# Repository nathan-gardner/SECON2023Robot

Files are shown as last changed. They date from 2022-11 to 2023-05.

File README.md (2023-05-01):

# **SECON2023Robot - IEEE SoutheastCon Robotics Competition**

## **Final CAD Model for Competition Robot**

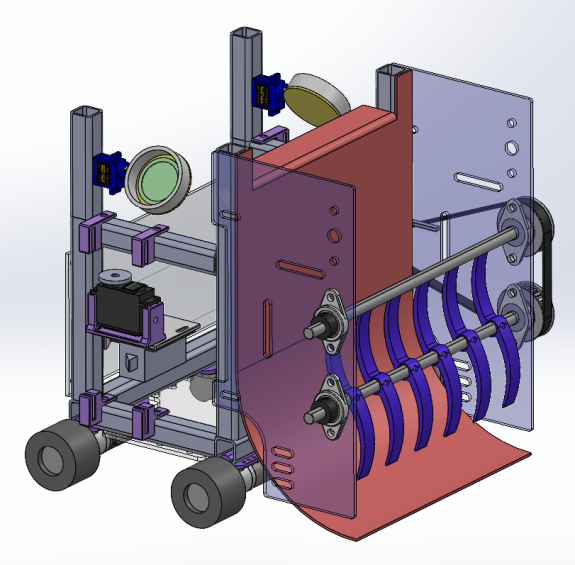
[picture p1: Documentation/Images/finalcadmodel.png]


## **Executive Summary**

The purpose of this project is to build a robot that will be sent to the SoutheastCon student competition in Orlando, Florida. This robot will represent Tennessee Technological University to schools around the Southeastern United States. This document will include further details on the team’s design for the project.

The autonomous tasks the robot may attempt include the following: Feed manatees and alligators the correct food chips, relocate ducks to the duck pond, rebuild pedestals into statues, deposit any unused objects into the recycle bin, and play an animated fireworks video at the end of the round.

The robot was rescoped throughout the year and just before the competition to be able to meet objective and once we know opponents capabilities at the competition. The final robot implemented was able to feed manatees and alligators the correct food chips, relocate ducks to the duck pond, and to push remaining items to the recycling areas. 

The team placed fourth out of thirty six schools in the competition, which is the second best performance in Tennessee Tech history. The team sees this as a success considering the ordering setbacks experienced by all the Capstone teams during the Spring 2023 semester, and the scope changes that were necessary to meet deadlines for the competition. 

Full rules document available [here](/Documentation/IEEE-SoutheastCon-2023-Hardware-Competition-Rules-v3.0.pdf).

## **Capabilities**

The [signoffs](/Documentation/Signoffs/) include function of the subsystem, constraints, buildable schematics, analysis, and bill of materials.

Capabilities of this project are described in signoffs with clear indication of what subsystem progressed through the research phase, which made it into development, and which subsystem were implemented into the robot which went to competition.

The path that this robot follows is defined in [top_level.py](/Software/top-level/top_level_package/scripts/top_level.py) and is all relative to the starting area. The distance is measured using encoder clicks and directions are published within the ROS computation graph. This means the robot cannot observe its surroundings and react to its surroundings, but can only go point to point based on the code within that top_level.py file. This was fine for our street sweeper implementation, and was a necessity in design because none of our vision sensors that we ordered came in the mail. This path implementation was reliable across runs. The direction publications were formatted as ROS Twist messages which gave direction and velocity in rotations per minute. The RPM was maintained on the Arduino using a custom PID controller written in C++. 

## **Salient Outcomes**

The team believes that one salient outcome of this project is a platform for understanding robot operating system for future SECON competitions at Tennessee Tech, and other robotics projects undertaken by capstone groups at the University. This is specifically referring to the TCP/IP network communication established in this project between the Jetson Nano and Arduino Mega2560. 

This project was the closest ever integration of the Mechanical Engineering Department's Senior Design course and the Electrical and Computer Engineering Department's Capstone course. These courses are based around an all-encompassing project from what students have learned in University. The team and its advisors has learned a lot about what has worked and what can be improved with this format of project, and this lessons learned will be taken into the future with the students graduating and for those advisors with future groups.  

## **Project Demonstration & Images**

### **Video of Robot at Competition**

Video of robot at competition during the first round of semi-finals available [here](https://www.youtube.com/watch?v=IqyCZeEZ9IM).

### **Robot image**

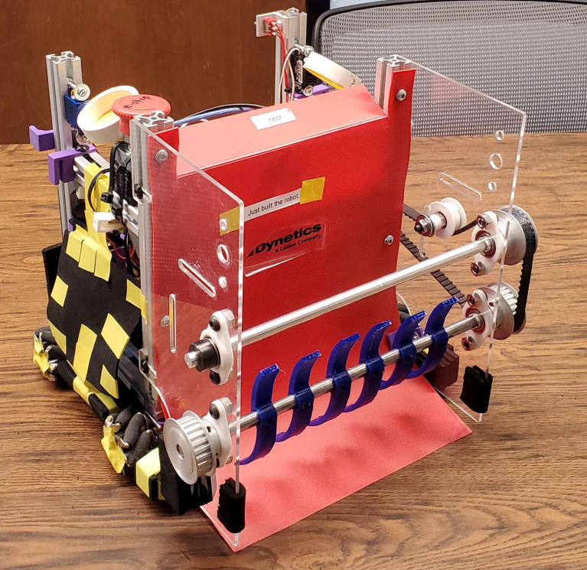
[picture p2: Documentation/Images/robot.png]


More images of the robot available [here](/Documentation/Images/robot/).

#### **Description of Arena:**

- Feeding areas - green and red rectangles in the left corners of the arena
- Starting area - White square in the bottom center of the arena
- Duck Pond - Blue circle in the middle of the top section of the arena
- Recycling areas - Striped white rectangles in the right corners of the arena
- Fireworks switch - Silver rectangle on the right side of the arena
- Inner circles - Three located to the left and right of the starting area, as well as in the middle of the duck pond

#### **Areas utilized for points during competition**

- Feeding areas - Most of our teams points came from correctly delivering the food chips to the feeding areas consistently.  
- Recycling areas - Where the robot pushed loose and randomly placed items to gain points. 
- Duck pond - Ducks ended up in the duck pond during competition. This counted for points on the scoreboard. 

## **Subsystems**
- [Feeding](/Documentation/Signoffs/LukeMcGill-signoff-Feeding.md) - Delivered chips to correct area using servos.
- [Locomotion](/Documentation/Signoffs/LukeMcGill-signoff-Locomotion.md) - Transported robot using mecanum wheels.
- [Power](/Documentation/Signoffs/MarkBeech-MadisonKelly-signoff-Power.md) - Powered every system with two 6V batteries and a 12 V battery.
- [Low-level Controller](/Documentation/Signoffs/NathanGardner-signoff-LowlevelController.md) - Arduino Mega2560 was selected as the main motor controller. 
- [Top-level Controller](/Documentation/Signoffs/NathanGardner-signoff-ToplevelController.md) - Nvidia Jetson selected for computation power as compared to Raspberry Pi.
- [Delivery System](/Documentation/Signoffs/Team2-signoff-ConsumptionSubsystem.md) - pushed objects outward when near a recycling area.

## **Cut Subsystems with explanation**
- [Vision](/Documentation/Signoffs/Fatima-signoff-vision.md) - Sensors were not received in time for building. The team ordered LIDAR sensor and color sensors and they never arrived.
- [Duck Storage](/Documentation/Signoffs/MadisonKelly-signoff-DuckStorage.md) - Subsystem cut as part of the rollback a few days before the competition. We did not have consistency in delivering the ducks stored to the duck pond reliably. A risk reward analysis was done and it was voted on by the team to remove the subsystem entirely. 
- [Pedestal Storage and Delivery](/Documentation/Signoffs/MadisonKelly-signoff-PedestalStorageAndDelivery.md) - Parts were not received in time for building. 
- [Sorting](/Documentation/Signoffs/MarkBeech-signoff-Sorting.md) - Parts were not received in time for building. Sorting was cut when rescoping once we realized we were not receiving parts for many of the subsystems we ordered. 
- [Consumption -> Delivery Subsystem](/Documentation/Signoffs/Team2-signoff-ConsumptionSubsystem.md) - Rescoped 24 hours before the competition. The function was transitioned from consumption into the robot to ejection into the recycling area.  

## **Experimentation**

For each run, there were ten ducks and seven pedestals randomly distributed on the arena as well as six food chips (3 red and 3 green) that the team could pre-load before the run started. The team had three minutes after the start switch was flipped to get as many points as possible. The results from these runs are shown below.



| Round | Green chip | Red chip | Cylinder Recycle | Duck Recycle | Duck Pond | Grand Total Points |
| ----- | --- | --- | --- | --- | --- | --- |
| 1 | 3 | 3 | 1 | 4 | 0 | 52 |
| 2 | 3 | 3 | 0 | 0 | 0 | 42 |
| 3 | 2 | 3 | 0 | 0 | 0 | 35 |
| 4 | 2 | 2 | 4 | 6 | 0 | 48 |
| 5 | 3 | 3 | 4 | 1 | 0 | 52 |
| 6 | 2 | 2 | 1 | 2 | 1 | 39 |

Below is the number of points scored in each round of the competition. If we had integrated the all functionality targeted after the rescope, we would have scored 86 points each round. 

Recycling: $2\ points * 17\ objects = 34\ points$

Feeding: $6\ correct chips * 7\ points = 42 \ points$

Fireworks: $1\ fireworks\ switch\ flip * 10\ points = 10\ points$

Total: $86\ points$



**Full experimentation document available [here](https://github.com/nathan-gardner/SECON2023Robot/blob/main/Reports/Experimentation.md).**

## **About Us**

### **Team Image**



**Names from left to right:** Grayson Vermillion, Carlos Salvatierra, Ethan Lewis, Mark Beech, Luke McGill, Nathan Gardner, and Madison Kelly.

### **IEEE Hardware Team**

**ECE team**

Nathan Gardner is an undergraduate Computer Engineering student and is currently a Senior at Tennessee Technological University. Nathan is Team Lead/ Captain for the Southeastcon Robotics Competition Hardware Team. Nathan was responsible for the low-level and top-level controller subsystems and worked on most of the  software implementation for the robot. 

Madison Kelly is an undergraduate Electrical Engineering students and is currently a senior at Tennessee Technological University. Madison is the Project Manager for the Southeastcon Robotics Competition Hardware Team. Madison was responsible for the storage subsystems and was partially responsible for the power subsystem along with Mark Beech.

Fatima Al-Heji is an undergraduate Computer Engineering student and is currently a senior at Tennessee Technological University.

Luke McGill is an undergraduate Electrical Engineering student and is currently a Senior at Tennessee Technological University. Luke was responsible for the locomotion and feeding subsystems. Luke also worked on the software implementation for the robot.

Mark Beech is an undergraduate Electrical Engineering student and is currently a senior at Tennessee Technological University. Mark was responsible for the sorting subsystem and was partially responsible for the power subsystem along with Madison Kelly.

**ME team**

Grayson Vermillion

Carlos Salvatierra is an undergraduate Mechanical Engineering student at Tennessee Technological University. Carlos is a member of the Southeastcon Robotics Competition Hardware Team. Carlos is responsible for creating the robot chassis and drivetrain. Carlos has years of experience working with and leading various high level robotics teams in the past.

Ethan Lewis

### **Faculty Supervisor**

Mr. Jesse Roberts

### **Stakeholders**

The Institute of Electrical and Electronics Engineers (IEEE) is the organization that is hosting the competition in Orlando, Florida on April 13-16th, 2023. Stephen Hopkins is the chair of the hardware competition. Tommy Dillen from Valencia College is the leader of Valencia IEEE Student Chapter design team and designed the arena for the competition.

At the competition, the team will represent the Tennessee Tech ECE Department by showing the skills acquired over most of the ECE curriculum.

Tennessee Technological University's College of Engineering's reputation will be affected by our presence and performance at the competition.

## **Repo Organization**

Below is the layout of the repo.

### **Reports**

Reports are attached in the Reports folder, linked below, and are named "Team2_(NameOfDocument)".

[Reports](/Reports/)

### **Documentation**

The [3D Models](/Documentation/3D%20Models) folder contains any CAD models there might be.

The [Electrical](/Documentation/Electrical) folder contains all electrical schematics.

The [Images](/Documentation/Images) folder contains images of the subsystems.

[Signoffs](/Documentation/Signoffs) folder contains the completed signoffs for each subsystem.

##### **Main Documentation Folder**

[Documentation](/Documentation/)

### **Software**

We will use language and Google (.clang-format) standard programming practices when writing software. We will document our code using Doxygen markdown and commenting style for readability. 

[Software](/Software/)

_Note: This repository was publicly archived on April 30th, 2023_

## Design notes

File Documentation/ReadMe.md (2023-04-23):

# Documentation

## Signoffs

Signoffs are the detailed design documents for the project. They include detailed specification, buildable pdf schematic, analysis, and the bill of materials. Analysis is performed on components to prove that they are sufficient and will likely work. The signoffs that are in main have been approved by the supervisor, Mr. Jesse Roberts. Signoffs are included in a marddown file [here](/Documentation/Signoffs/). 

## Final set of prints (final design artifacts)



### 3D Models

3D models are included [here](/Documentation/3D%20Models/).

The 3D models section will be updated throughout the project to reflect what has been signed off and designed. 

### Wiring Schematics

Electrical wiring schematics available [here](/Documentation/Electrical/Schematics/).

The wiring schematics section will be updated throughout the project to reflect what has been signed off and designed. 

#### PCB files

Electrical wiring PCBs available [here](/Documentation/Electrical/PCB/).

The PCB files section will be updated throughout the project to reflect what has been signed off and designed. 

## Final BOM

Final BOM available [here](/Documentation/BOM/TotalBOM_Final.pdf).

## Datasheet 

Each subsystems datasheet is essentially the signoff for that subsystem. The final datasheet will be created near the end of the project when the design is complete.

Final Datasheets for each subsystem available [here](/Documentation/Signoffs/).

## The project poster

Final poster available [here](/Documentation/Poster/IEEE%20SECON%20Hardware%20Competition%20Team%20Final%20Poster.pdf).

## Detailed photos of the project

Detailed photos for the project are available [here](/Documentation/Images/).

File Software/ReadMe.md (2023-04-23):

# Software

Project source code is stored here. Below is an explanation of each file and how it functioned in the project.

Further documentation on each project can be found in comments/doxygen in the source code. 

## **Files**
- [demo](/Software/demo/) - Initial PlatformIO project created in testing. This was used to setup ROSSerial and to confirm that we would be able to use ROSSerial to pass messages between the Nvidia Jetson and the Arduino Mega as we had planned in design.
- [matlab-sim](/Software/matlab-sim/) - File for MATLAB simulations used during signoffs
- [mega2560](/Software/mega2560/) - PlatformIO Project that ran on the Arduino Mega during the competition. Mega functioned as the main motor controller and hardware interface device for this project.
- [top-level](/Software/top-level/) - ROS package with holds the script that ran on the Nvidia Jetson to command the robot to follow its path in the arena and actuate motors.
- [ultrasonic](/Software/ultrasonic/) - Ultrasonic demo that was created while the team was considering implementing ultrasonic in the project.

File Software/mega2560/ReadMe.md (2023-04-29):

# mega2560/mega1

## Software Function

PlatformIO Project that ran on the Arduino Mega during the competition. Mega functioned as the main motor controller and hardware interface device for this project.

## Dependencies

Operating system: 22.04.1-Ubuntu
IDE: VSCode
Extensions: PlatformIO
Required installations: ROS Melodic, rosserial

## How to Install

Step by step instructions for installation can be found below:

[VSCode](https://code.visualstudio.com/Download)

[ROS Melodic Installation](http://wiki.ros.org/melodic/Installation/Ubuntu)

[ROSSerial Installation](https://sites.duke.edu/memscapstone/using-rosserial-to-setup-a-ros-node-on-a-teensy/)

## Program Execution

This is a PlatformIO project and code can be uploaded to the Arduino using the upload button (->) on the command bar of at the bottom of the VSCode window. 



The following code is executed on the Nvidia Jetson (or comparable computer) to execute this program

```
# start ros master
roscore

# start rosserial
rosrun rosserial_python serial_node.py _port=[PATH_TO_ARDUINO_PORT] _baud=115200

# to start main top_level.py execution, navigate to top_level.py and run with python command
cd [PATH_TO_REPO]/Software/top-level/top-level-package/scripts
python top_level.py
```

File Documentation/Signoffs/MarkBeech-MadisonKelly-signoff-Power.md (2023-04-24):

# **Power Subsystem**
## **Function of The Subsystem** 
- Provides power to all other subsystems that require voltages and currents not supplied indirectly through the low-level controllers or the top level controller pins.
- Allows the robot to be turned off and on.
- Addition of an emergency stop button in order to meet safety standard and competition requirement.
## **Constraints** 
- The power supply must supply 12 V and a current of more than 2 A to accommodate all components that will be running at one time. 
- The output of the battery must be regulated with a DC-DC converter in order to ensure each component is provided with the proper voltage for operation.   
- Fuses will need to be added to the power supply bus for added overcurrent protection.
- Many of the loads will need to be stepped down to 6V and have a regulated output to eliminate ripple voltage. There will be filters to smooth out the ripple
- The ripple voltage from the inductive load of the motors should be eliminated in order to protect other components. To mitigate this, the team will add smoothing capacitors on each motor load.
- Voltage input ranges for all components can be seen in the table below.
- Since there are multiple loads that need 12V and 6V supplied, there will need to be a power bus for each of them. The power bus selected is rated up to 10A.
- The power supply chosen has a 5V USB output. Because of this, the concerns for powering the Nvidia Jetson as well as both arduinos will be separate from the remainder of the components. 
- An emergency stop button must be used for the safety of those involved in the competition. 
  - The emergency button must have a flyback diode attached in reverse bias because of the motor’s inductive load and the chance of a sudden switch in the power being supplied.

### **Constraint from Standard**

- Shall have a self-latching emergency stop push-button that has a positive operation. The button shall not be a graphical representation or a flat switch based on NFPA 79 - 10.7.2.

### **Voltage input ranges for all components**

| Component | Input Range |
| --- | --- |
| DC-DC converter | 9V to 18V |
| Buck Converter board  | 4.0 to 40V  |
| L298N | 5V to 35V |
| TB9051FTG | 4.5V to 28V |
| Micro Maestro | 5V  to 16V  |
| Lock style solenoid | 9V to 12V |
| Nvidia Jetson nano | 4.75 V to 5.25 V |

### **Voltage and current requirements for all components**

| Subsystem | Component | Voltage (V) | Current (A) |
| --- | --- | --- | --- |
| Locomotion | Motor Drivers (2) | 12 | 1.2 |
| Consumption | Motor Driver | 6 | 0.5 |
| Duck Storage and Delivery | Solenoid Actuator | 12 | 0.65 |
| Pedestal Storage, Duck Storage, Sorting, and Feeding | Servo Motor Controller | 6 | 2.17 |
| Sorting | Motor Controller | 6 | 0.25 |

### **Voltage and current requirements for all continuous components**

| Subsystem  | Component | Voltage (V) | Current (A)  |
| --- | --- | -- | ---- |
| Locomotion  | Motor Drivers - Motors (4) | 12 | 1.2  |
| Consumption | Motor Driver - Motor | 6  | 0.5  |
| Sorting | Motor Controller | 6  | 0.25 |

## **Buildable Schematic**

### **CAD Model for the subsystem:**

Shown below is the layout of the robot. The compact size of this power supply (shown in red) should allow for plenty of room for other components as needed.



### **Electrical Schematics:**

All electrical circuits will be implemented via soldered breadboard.

**Initial electrical schematic**



**Final implementation electrical schematic**



## **Analysis**

### **Power Supply - 12V Output** 

The power supply can supply 12 V at 6000 mAH and 5 V at 12000 mAH and the maximum current output is 3A. Since each competition round is only 3 minutes, the following calculations were performed. 

$Time = \frac{6000\ mAh}{3\ A} = 2\ hours = 120\ minutes$

$rounds = \frac{120}{3} = 40 rounds$

The robot should be able to run up to 40 rounds without needing a charge. This will help with testing as well as reducing the risk that the robot's power supply will die during the competition.

### **Current Analysis**

#### **Block Diagram for all components**



Currents have been labelled for use in a matlab script detailed below. Each current value listed by each component was found from the components datasheet.

#### **Block diagram for all constant loads**



#### **Matlab Simulation**



This simulation was done using the block diagram for all constant loads shown above.

This calculates the currents going into each branch and adds them together to find the total current needed to be supplied by the power supply. This was done while taking into account the efficiencies of the buck converter and the DC-DC converter.

According to the MatLab simulation above the total current needed to be supplied by the power supply is 1.767 A. The power supply chosen has a max output current of 3 A, which is almost double the constant current constraint.

### **DC-DC Converter**
This power supply has an output range from 9 - 12.6 V with a typical value of 11.1 V. This is why a DC-DC converter is needed to regulate the input to 12 V. The concern for noise produced by the buck converter is adressed in an LTSpice simulation shown below.

The power supply itself has a ripple of 100 mV, which is not a problem for this DC-DC converter as it can accept anywhere between 9 - 18 V.



According to the datasheet for the DC-DC converter chosen, the ripple noise has a peak to peak ampliture of 150 mV and a switching frequency of 270 kHz. The noise has been modelled as such and can be seen in the LTSpice model above (This noise was measured by the manufacturer with a $1 \ \mu F$ ceramic capacitor in parallel with a $10 \ \mu F$ electrolytic capacitor, which can be added to the circuit if necessary)



Above is the unregulated noise before passing through the filter. The filter will be implemented via a solderless breadboard.



Above is the output voltage after the filter. The voltage appears to be much claner and varries very close to exactly 12 V.

### **Buck Converters**
The buck converter boards were found on Digi-key. The board uses the LM2596 voltage regulator IC and, according to the datasheet provided by Digi-key for the board, it is suitable for our application.

Noteable specs include:
- Input voltage: 4 - 40 V
- Output voltage: 1.5 - 37 V
- Max output current: 3 A
- Max output power: 20 W
- Switching frequency: 150 kHz
- Adjustable via screw potentiometer
- built in voltmeter

Buck converter boards will be used to drop the 12 V supply voltage to 6 V for all components needing 6 V to operate. These buck converters are shown on the electrical schematic above. 

According to the datasheet for the LM2596 part, a typical output ripple voltage can range from approximately 0.5% to 3% of the output voltage. This means The output ripple at worst case will be:

 $0.03(6) = 0.18 \ V = 180 \ mV$



Above is an LTSpice simulation of the noise ripple that could result from the buck converter board. The device has a switching frequency of 150 kHz as reflected in the model.



Above is the unregulated noise signal with $V_{p-p} = 180 mV$ and a frequency of 150 kHz. A LC filter with a diode will be implemented on a solderless breadboard to flatten out the voltage.



As shown above the output voltage is regulated to 6 V with a small ripple of less than 1% of the output voltage.

### **Motor Ripple**

All motors chosen in this project have come from Pololu. Pololu recommends connecting up to three $0.1 \mu F$ capacitors to the motors. It was recommended that one cap should be connected from the positive lead to the case, one from the negative lead to the case, and one across the input terminals.

### **Power Bus**

Since there are many components that need 12V and 6V, there will be at least two power buses to better distribute the power to the correct components within the robot. The buses selected are rated up to 24V, and 12V is the maximum voltage within the robot. Also, the number of outputs on the bus itself is much greater than the number of outputs the team will need. Therefore, the buses selected will be sufficient. 

### **USB Output Power**

The Nvidia Jetson Nano Dev kit will be power via the USB-A port on the power supply connected to the Jetson's micro USB port. This supply has a ripple of 100 mV on this output as well, meaning the output can be from 4.9 V to 5.1 V per the image below sent from the manufacturer via email. 



The Jetson requires anywhere from 4.75 V to 5.25 V to operate, meaning it can run even with the ripple of 100 mV. As for current, the power supply is rated for up to 2 A, which is what the Jetson requires.

### **Emergency stop button**

The emergency stop button will need to have a flyback diode connected to the two output lines of the button to prevent sudden voltage spikes when current is interrupted.

The E-stop button was chosen to be a 2 channel normally closed switch. This was chosen so power can be broken from locomotion, consumption and sorting all together with one button as shown in the electrical schematic above. 

## **BOM**
| Name of Item | Description | Used in which subsystem(s) | Part Number | Manufacturer | Quantity | Price | Total  |
|---|---|---|---|---|---|---|---|
| Rechargeable 12 V Battery | 12 V/6000 mAH Lithium Ion Battery Pack | Power | YB1206000-USB  | TalentCell | 1 | 39.99 | 39.99  |
| Buck Converters | DC-DC Adjustable Buck Converters 3-40V to 1.5-35V | Power | LM2596 | ATNSINC | 3 | 15.69 | 47.07  |
| E-Stop Button | Self-Locking Emergency Stop Button 2 NC Red Mushroom 660 V 10 A | Power | HB2-BS544 | MXUTEUK | 1 | 10.99 | 10.99  |
| 3 A Fuses | 3A 250V Fuses (pack of 20) | Power | F3AL250V | BOJACK | 2 | 5.99 | 11.98  |
| 1N5822 Diode | Ximimark 100Pcs 1N5822 Schottky Diode 3A 40V DO-201AD (DO-27) Barrier Rectifier Diode for Household Appliances | Power | 1N5822 | Ximimark | 1 | 7.29 | 7.29 |
| 0.1 uF Capacitors | E-Projects - 0.1uF Ceramic Disc Capacitor - 50 Volts (25 Pieces) | Power | 0.1 uF | E-Projects | 1 | 5.99 | 5.99 |
| 1 uF Capacitor | 1 µF Conformal Coated Tantalum Capacitors 50 V Radial 8Ohm | Power | TAP105K050SCS  | KYOCERA AVX | 1 | 0.82 | 0.82 |
| 330 uF Capacitors | Capacitor 4.7UF 6.8UF 10UF 15UF 22UF 47UF 100UF 220UF 330UF 470UF 680UF 1500UF Electrolytic Capacitors Kit 6.3V 10V 16V 25V 35V 50V 100V 400V,295Pcs | Power | 330 uF | changhe | 1 | 18.98 | 18.98  |
| 33 uH inductors | uxcell 50Pcs 0510 Color Ring Inductor 33uH 1W Axial RF Choke Coil Inductor | Power | 33 uH | uxcell | 1 | 8.49 | 8.49 |
| DC-DC Converter | DC DC Converter 12 V 120 W | Power | 209-JCK4012S12 | XP Power | 1 | 71.5 | 71.5 |
| Power Distribution Bus | Solid Brass | Power | 737 | Adafruit | 5 | 1.95 | 9.75 |
| Total | | | | Total Components | 16 | Total Cost | 232.85 |

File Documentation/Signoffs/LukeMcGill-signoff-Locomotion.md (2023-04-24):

# Locomotion Subsystem
## Function of the Subsystem
- Transport the robot no less than 0.0677 m/s

- Ensure that the predetermined path can be traversed in the allotted time of three minutes

- The top level controller communicates with the low level controller through USB. The low level controller will then send a PWM signal to the motor driver, which will control the motor's speed. The low level controller will also send a digital signal to the motor driver that will control the direction of the motor.

## Constraints
- Weight of the robot ( $\approx$ 10.376 kg)
- Minimum travel speed required (0.0677 m/s)
- Motor torque required (0.0604 Nm per motor)

### Socioeconomic Consideration
- Motor chosen will operate at $\approx$ 70% of it's maximum efficiency. This will help conserve power and reduce battery charging costs.

## Buildable Schematics

### Motor


The two motor encoders will tell the low level microcontroller how fast the motor is driving, as well as the direction. These will be used in the path planning process.

### Electrical Schematic
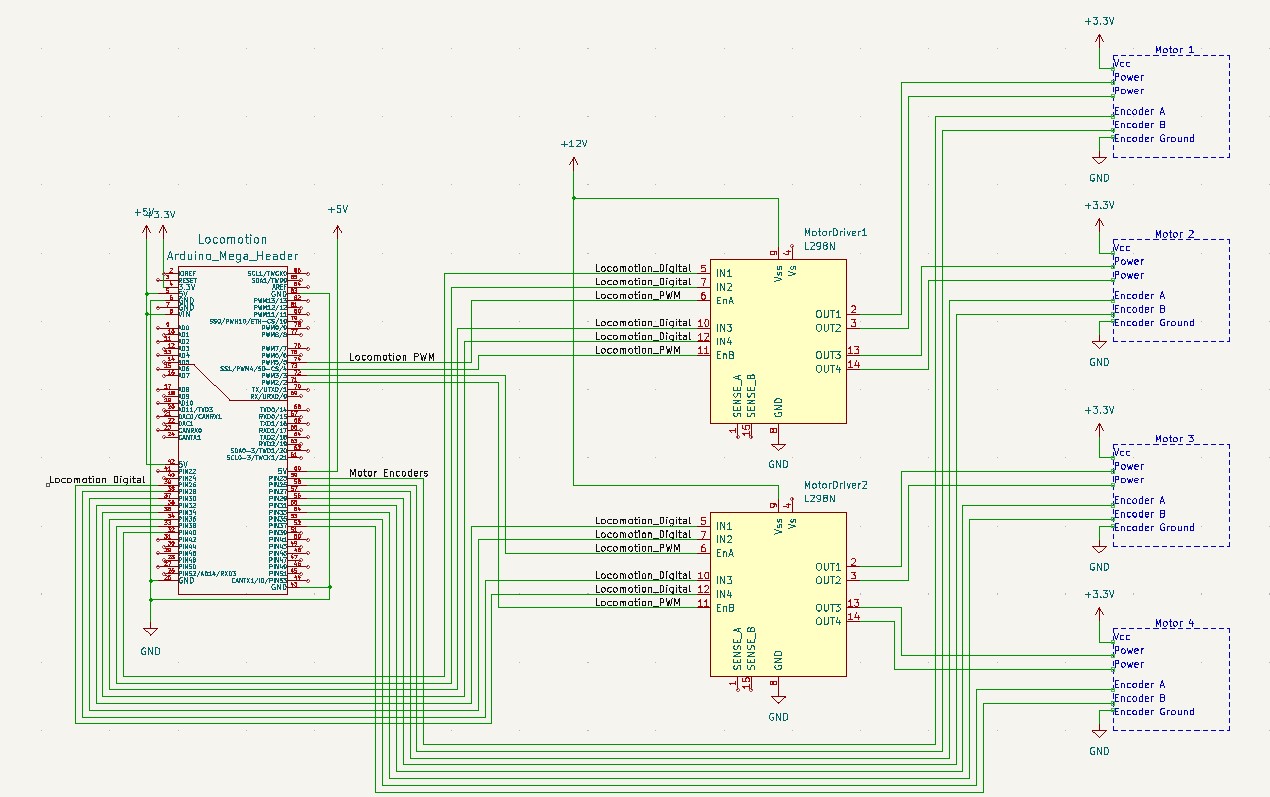
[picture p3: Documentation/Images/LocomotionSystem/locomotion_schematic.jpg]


The electrical schematic can be found [here](https://github.com/nathan-gardner/CapstoneRepo/tree/main/Documentation/Electrical/Schematics/Sources/Locomotion):

### Locomotion Assembly
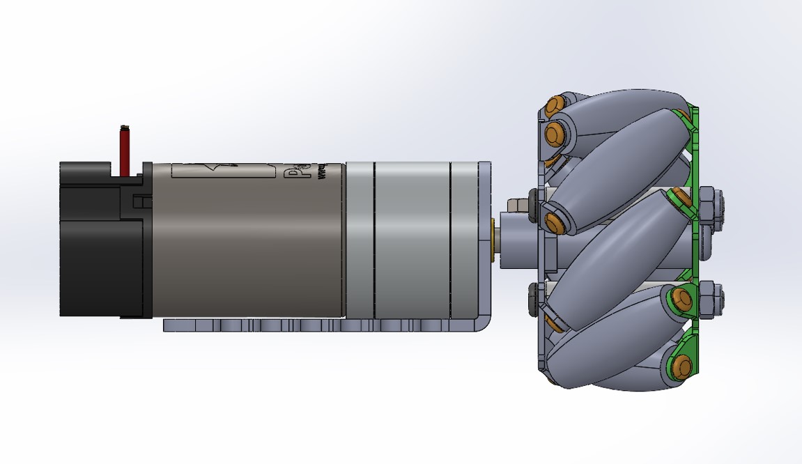
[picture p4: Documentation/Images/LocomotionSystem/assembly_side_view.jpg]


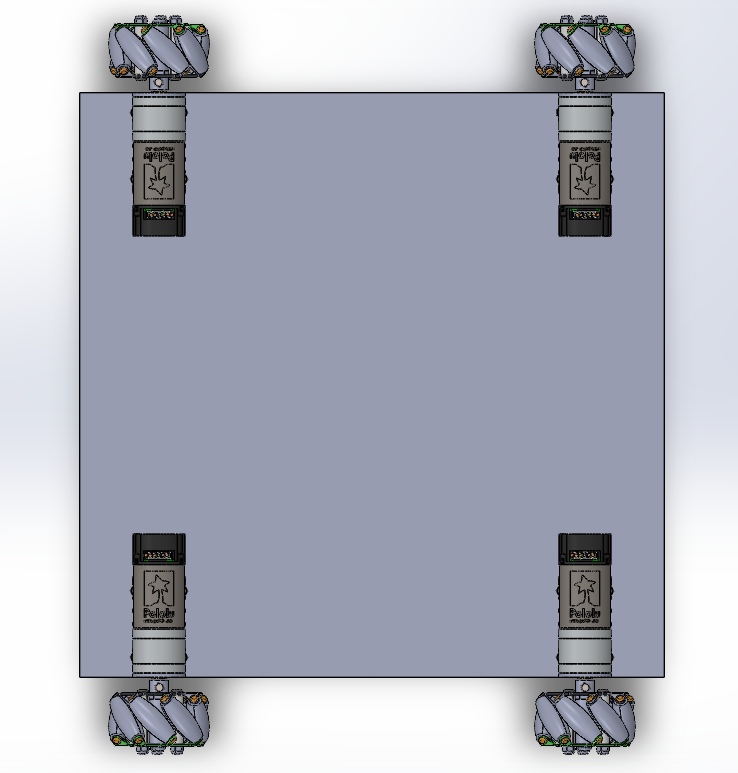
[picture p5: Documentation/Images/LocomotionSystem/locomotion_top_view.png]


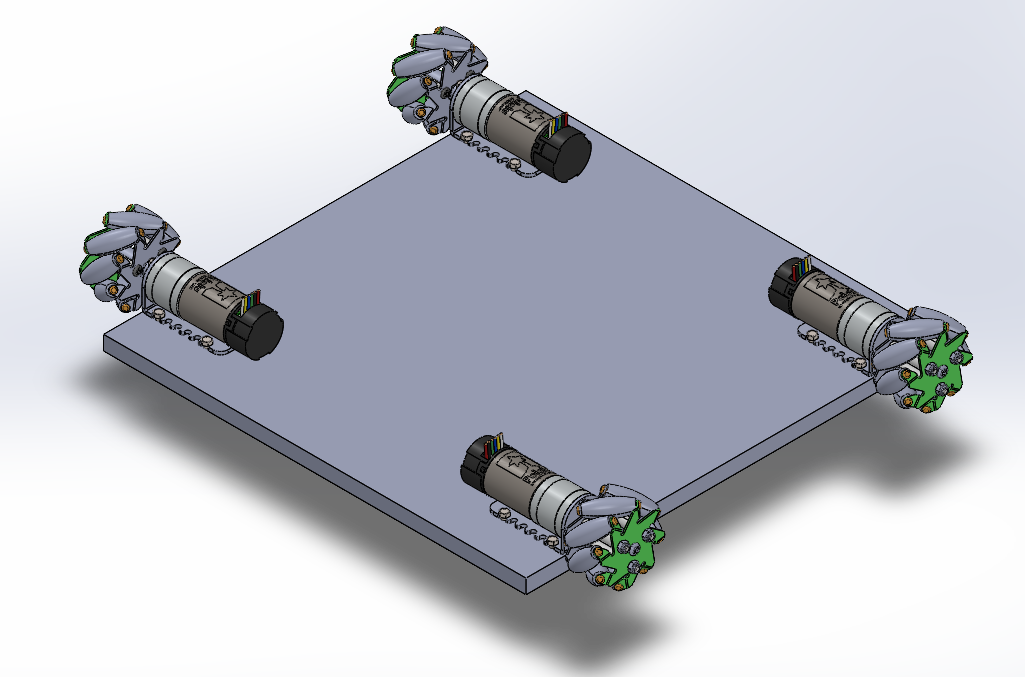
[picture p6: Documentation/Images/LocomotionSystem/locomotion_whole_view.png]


Each motor will have a motor mount. The mount will attach to the motor by two screws. The motor and mount assembly will attach to the chassis by four screws. Please note that the chassis has not been designed yet, so the model does not show the final product, rather how the motor assebmly will be mounted.

The CAD model for the motor and wheel assembly can be found here.
https://github.com/nathan-gardner/CapstoneRepo/tree/main/Documentation/3D%20Models/LocomotionSystem

## Analysis
### Acceleration

In order to traverse the entire playing field within the three minute time limit, the robot needs to move no slower than 0.0677 m\s. However, to allow for two minutes to complete the other tasks, the fastest velocity needed will be 0.2023 m/s. This would be the worst case scenario.

$v = 0.2023\ m/s$ 

$a = \frac{v - v_{o}}{t}$

$a = \frac{0.2023 - 0}{1}$

$a = 0.2032\ m/s^2$

### Force
#### Main Robot Weight
$W_{Motors} = 0.606\ kg_f$

$W_{ConsumptionParts} \approx  1.128\ kg_f$

$W_{Controllers} \approx 0.129\ kg_f$

$W_{Bolts} \approx 0.366\ kg_f$

$W_{Walls} \approx 1.669\ kg_f$

$W_{Power Supply} \approx 1\ kg_f$

$W_{Miscelaneous} \approx 4\ kg_f$

$\ $

#### Robot Caboose Weight
$W_{Ducks} = 0.708\ kg_f$

$W_{Pedestals} = 0.1442\ kg_f$

$W_{Walls} \approx 0.626\ kg_f$

$\ $

#### Total Weight

$W_{Total} \approx 10.376\ kg_f$

$M_{Total} \approx 1.0588\ kg_m$

$\ $

$\mu_{s} = 0.95$ (wood on rubber)

$\Sigma F_x = ma$

$F_n = mg = W_T$

$\Sigma F_x = F - (\mu_{s}F_n)$

$ma_x = F - (\mu_{s}F_n)$

$1.0588 * 0.2023 = F - (0.95 * 10.3762)$

$F = 10.07\ N$

$\ $

### Torque
$r = 0.024\ m$

$\tau_{total} = rFsin(\theta)$

$\tau_{total} = 0.024 * 10.07*sin(90^\degree)$

$\tau_{total} = 0.2417\ Nm$

$\tau_{motor} = \tau_{total} / 4 $

$\tau_{motor} = 0.0604 \ Nm$

$0.0604\ Nm = 6.149\ kgmm$

$\ $



The chosen motor is the Pololu #4865. It is a 12V medium power motor. The required torque for each motor is 6.149 kg-mm. This motor has a max efficiency at 8.6 kg-mm of torque. At 6.149 kg-mm of torque, the motor will operate at $\approx$ 70% of it's maximum efficiency. This motor choice will allow the torque requirments to be met while simultaneously achieving high efficiency. The motor draws 0.28 A. The L298N motor driver supplies 2A which is more than enough for this motor. The maximum torque of each motor is 40 kg-mm.

$6.149\ kgmm / 40\ kgmm = 15.34$\%

$100$\% $- 15.34$\% $= 84.66$\%

At the current torque requirment of 6.149 kg-mm of torque, only 15.34\% of the motor's torque capacity is being used. This allows for 84.66\% of each motor's torque capacity as the margin of safety.

## BOM
| Name of Item | Description | Used in which subsystem(s) | Part Number | Manufacturer | Quantity | Price | Total  |
|---|---|---|---|---|---|---|---|
| Mecanum Wheel  | Mecanum wheels will allow the robot to move and turn in any direction (pack of four wheels) | Locomotion | 14209 | Nexus Robot | 1 | 41.48 | 41.48  |
| Wheel Coupling | The wheel couping attaches the wheel to the motor | Locomotion | 18077 | Nexus Robot | 4 | 2.34 | 9.36 |
| Motor | The motors will drive the wheels allowing the robot to move | Locomotion | 4865 | Pololu | 4 | 45.95 | 183.80  |
| Motor Mount | The motor mount will secure the motor to the chassis (pack of two mounts) | Locomotion | 2676 | Pololu | 2 | 7.95 | 15.90 |
| Motor Driver | The motor drivers supply the voltage and current requirements of the motor (pack of 4) | Locomotion | L298N | ST | 1 | 7.41 | 11.39  |
| Total | | | | Total Components | 13 | Total Cost | 261.93 |

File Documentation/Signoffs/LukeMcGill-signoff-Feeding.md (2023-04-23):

# Feeding Subsystem - revised 4/6/2023

## Function 

~~- Deliver the correct chip to the correct area based on color~~

~~- Color will be detected with the color sensor from vision subsystem~~

~~There will be rectangles in the left corners of the arena which will be green (0x00FF00) and red (0xFF0000). Green signifies the manatees and red signifies the alligators aquarium. A color sensor will be pointed towards the ground and will detect the color of the aquarium, and spin the servo the correct direction in order to drop the right color chip through the false bottom on the feeding subsystem. This will allow the servo positions to be preprogrammed, so that the robot can react correctly to the different colored aquariums. The servo will be connected to a plate that will hold the chips up, but when the servo is actuated to a specific orientation, the chips will fall through a hole onto the floor of the arena and into the correct aquarium. The chips will sit in a sort of silo, and will be held up by a plate connected to the servo. The servo will rotate clockwise or counterclockwise, which will allow the chips to fall through a false bottom and onto the aquarium area.~~

~~The position of the aquariums can be reflected based on the arena we are playing in, this is the reason for the design choice of making the robot detect the color before dispersing the chips onto the playing field.~~

- Deliver the correct chip to the correct area

There will be rectangles in the left corners of the arena which will be green and red. Green signifies the manatees and red signifies the alligators aquarium. The robot will drop the chips in their respective areas based on the teams' placement before the competition. The servos will activate when they reach their pre-determined destination on each animal area. There will be two servos mounted on either side of the robot that will hold either red or green chips in a small "cup". Once they reach their destinations, the servos will turn about 180&deg; and dump the chips out of the cups, leaving the chips behind.

The competition rules allow for the feeding chips to be preloaded into the robot, so someone on the team will load the color chips into the feeding subsystem before the start of each round. One of the two silos will be loaded with green chips and the other of the two silos will be loaded with red chips. 

## Constraints

~~- The size of this subsystem will have to be such that it takes up only enough space to fit the chips (6.15 $in^3$) and allow space for the rest of the components on the robot. Analysis for the allowable size of feeding system is in analysis, with CAD models showing subsystem fit within the robot.~~

- The servos with the chip cups attached will be mounted towards the top of the robot in order to allow for some much needed space within the robot. The cups they are held in are 1.5 in diameter by 5 in height. Since they are mounted towards the outer edge on the top, they will not be taking up much space inside the robot.
- The servo motors must be as small as possible, while also providing necessary torque. The torque needed is 0.0494 $N \ast m$, so micro servos can be used. The calculation for the needed torque is below in analysis.

## Buildable Schematic

**Initial buildable schematic**



A closer look at the plate that the chips will sit on is below.



The layout of the chassis is below showing the major subsystems and their placement within the robot. This subsystem is titled "chip dispenser" or "chips". 

chassis

**Final implementation buildable schematic**

The chip dispensers can be seen near the top of the robot. They are the cups that are connected to servos. 



Below are images showing how all of the subsystems, including the feeding subsystem will fit into the robot.

Top view



Rear Side view 1



Rear Side view 2



Rear view



Front corner



Chassis Subsystem Fit CAD model files available [here](https://github.com/nathan-gardner/CapstoneRepo/tree/main/Documentation/3D%20Models/Chassis/Chassis_Fit).

## Electrical Schematic

The electrical schematic for the feeding subsystem is shown below. 



## Analysis

### Size

~~The dispensers that the chips will be stored in must be able to fit the chips. There will be three chips of each color, so the chips must be able to be stacked to a height of three in each silo.~~ 

Chip Size $= 1.5 in \ast 0.1 in$

~~Dispenser Interior Size $= 4.5 in \ast 0.15 in \ast 1.5 in$~~

Dispenser Interior Size $= \pi \ast 1.5 in \ast 0.5 in = 0.88 in^3$

Therefore, the chips will comfortably fit inside the cups. ~~This part will also be 3D printed, so the sizing can be adjusted during testing. The chips will fit into the silos in a way similar to how chips fit into a game of Connect 4, they will be top loaded and sit so that the diameter of the chip, $1.5 inches$, is the height of the chip when it is loaded into the silo.~~ 

### Motor Torque

The motor will only need to push the weight of the ~~small 3D printed plate.~~ cups with the chips inside. The volume of the 3D printed chips are calculated and modeled as a cylinder below:

$V = \pi r^2 h = \pi \ast 0.75^2 \ast 0.1 = 0.176715\ in^3$

The density of the TPU is $0.0448\ \frac{lb}{in^3}$, so the weight of the TPU printed chip will be $0.0448\ \frac{lb}{in^3} \ast 0.176715\ in^3 = 0.00792 lb = 3.59\ grams$. 

The downward force of the chips on the plate will be the mass of three chips times the acceleration of gravity squared. This would be $0.01077\ kilograms \ast 9.81^2 \frac{m}{s^2}^2 = 1.0365\ N$. The torque needed for the servo will therefore be $\tau = 1.0365\ N \ast 0.047625\ m = 0.0494\ N \ast m = 6.996\ oz \ast in$, and this based on the worst case moment arm measurement, derived from the picture below.



The torque of the motor selected is 21 oz-in, so it will be more than sufficient for its cause because it is three times minimum necessary torque from the calculations above. 

## BOM
| Name of Item | Description | Used in which subsystem(s) | Part Number | Manufacturer | Quantity | Price | Total |
|---|---|---|---|---|---|---|---|
| Servo Motor | FEETECH FS90 Micro Servo | Feeding |2818 | Pololu | 1 | 5.25 | 5.25 |
| Servo Motor Controller | Micro Maestro 6-Channel USB Servo Controller | Feeding, Pedestal Storage, and Duck Storage (included on Pedestal BOM) | 1350 | Pololu | 1 | 0 | 0 |
| Chip Tube | 3D printed 1.65 in x 0.5 in tube to hold the chips | Feeding | N/A | Print | 1 | 0 | 0 |
| Chip Stopper | 3D printed plate to stop the chips from falling | Feeding | N/A | Print | 1 | 0 | 0 |

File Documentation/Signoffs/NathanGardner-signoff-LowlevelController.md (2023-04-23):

# Low-level Controller Subsystem Signoff

## Function of the Subsystem

The specific function of the microcontroller network described in this signoff is its operation as the main hardware access controller. This means that this device is responsible controlling the logic to drive subsystem motors across the subsystem, but can be commanded directly by higher level systems. The main top-level microcontroller will be designed later and is not included in this subsystem. This top-level controller will be responsible for vision, robot path plan storage and logic to follow path, and most importantly be the ROS master controller device. 

The robot will be controlled via a microcontroller (MCU). The main constraints on the low-level main microcontroller subsystem are general purpose input/output (GPIO) constraints as well as computational constraints for general communication, vision communication, and object manipulation logic constraints. The microcontroller will generate Pulse-Width Modulation (PWM), digital, and interrupt signals to the various motor drivers and systems contained within the peripheral subsystems. 

The low-level microcontroller subsystem is essentially the low level nervous system of the robot, and the top-level controller (designed later) is like the brain of the robot. Consideration is taken below for how fast the robot needs to "react" or retrieve, process, and store data. In most cases in this implementation, this will be designed to mitigate issues with the real-time requirements of the robot. Issues could arise from not being able to gather and process information quickly enough from GPIO that is driven by a peripheral sensor. This subsystem is dependant on the sensors chosen for the design, but worst case constraints will be assumed in many cases (more GPIO than required, higher processing speed then required, etc.) so that the requirements are met in the final design. 

## Constraints

The low-level controller subsystem has constraints that it must abide by to be successful. The first and foremost is GPIO limitations, we will need enough GPIO to drive all the motors and read sensors and to interface with any other microcontrollers in the design. Power consumption will also be a constraint because the power system of the robot cannot be unnecessarily stressed in terms of power drawn from the controller. Available software will also be a constraint on the low-level microcontroller. All of these constraints are analyzed in the analysis portion of this signoff.

The direct interfaces between the controller and other subsystems are as follows:

1. Serial USB communication to the vision microcontroller. This will be a general USB port used to communicate objects which describe environment.
2. An input from the power system which triggers the microcontroller to start initializing code. This will be a digital input pin with hardware interrupt capabilities. 
3. Serial USB communication as an input to the object storage subsystem. This will be a output in terms of the microcontroller. 
4. PWM and digital logic high/low communication as an input to the object consumption subsystem. This will be a digital output pin in terms of the microcontroller.
5. The power input to the microcontroller, which will come from the power regulator in the power subsystem.  

Standard: IEEE 1118.1-1990 describes standards related to interdevice/intrabuilding as well as interconnection of microcontrollers. This standard will be reference and adhered to in terms of system controller interconnect design, which is part of the controller subsystem. 

Conceptual Design Document: [here](https://github.com/nathan-gardner/CapstoneRepo/blob/main/Reports/Team2_ConceptualDesignandPlanningFinal.pdf)

Number of motors that need to be driven and sensors that need to be read by the main controller and what purpose they serve are listed below.

### Two Low-level Mega Controllers (Locomotion, Fireworks, Feeding, Consumption and Sorting, Storage)

A design with two Arduino Mega 2560 Rev3 microcontrollers was selected in order to create a modular design and to allow for parallelization of the design amongst team members. This design also allows the design to come in well above the general IO requirement for each controller, which is covered in great detail below. 

Feeding subsystem - one motor that needs to be driven by the main microcontroller

| Feeding | | | | |
|---|---|---|---|---|
| | Pin Type  | Count | | |
| Activation for Arduino Nano | Interrupt | 1 | | |
| | | | Interrupt:  | 1 |
| | | | Total Pins: | 1 |

_Note: This Arduino Nano will need to be designed as part of the microcontroller network but will not be designed until the Feeding Subsystem is designed and will reflect the specific requirements of the Feeding Subsystem. It will be part of the Feeding signoff but will be part of the low-level controller network. This subsystem is standalone and a lower priority portion of the design. Right now all that is known is that the main Mega controller will generate a hardware interrupt which will invoke an interrupt service routine on the Nano._

_Interfaces needed:_ 
1. Motor for the rack and pinion subsystem

Fireworks subsystem - zero or one motor to flip the switch for the fireworks

| Fireworks | | | | |
|---|---|---|---|---|
| | Pin Type  | Count | | |
| Activation for Arduino Nano | Interrupt | 1 | | |
| | | | Interrupt:  | 1 |
| | | | Total Pins: | 1 |

_Note: This Arduino Nano will need to be designed as part of the microcontroller network but will not be designed until the Fireworks Subsystem is designed and will reflect the specific requirements of the Fireworks Subsystem. It will be part of the Fireworks signoff but will be part of the low-level controller network. This subsystem is standalone and a lower priority portion of the design. Right now all that is known is that the main Mega controller will generate a hardware interrupt which will invoke an interrupt service routine on the Nano._

_Interfaces needed:_ 
1. Servo control signal for flipping a switch if needed, will design to that need 

Locomotion subsystem - This subsystem will require four motors driven independently. We will need to use both encoder output A and B on all four motors to show direction of rotation. The table of the motor inputs that need to be driven by the motor are below.

| Locomotion | | | | |
|---|---|---|---|----|
| Motor Driver | Pin Type | Count | | |
| Speed | PWM | 4 | | |
| Forward Direction  | Digital  | 4 | | |
| Backward Direction | Digital  | 4 | | |
| | | | PWM: | 4  |
| | | | Digital: | 8  |
| | | | Total Pins: | 12 |

This means that four PWM pins will be needed and eight digital pins will be needed for the locomotion subsystem. 

_Interfaces needed:_ 
1. Control signal for four wheels, one PWM signal for speed, one for forward and one for backward direction, or twelve pins in total

Consumption Subsystem - Subsystem which will consume objects around the arena. Will be required to drive the motor driver for the object consumption subsystem. 

| Consumption  | | | | |
| --- | --- | ----- | --- | - |
| Motor Driver | Pin Type | Count | | |
| | Digital  | 2 | | |
| | PWM | 1 | | |
| Motor Driver | | | | |
| | Digital  | 2 | | |
| | PWM | 1 | | |
| | | | Digital: | 4 |
| | | | PWM: | 2 |
| | | | Total Pins: | 5 |

_Interfaces needed:_ 
1. PWM to control the speed of the motor that drives the object consumption system
2. Two digital pins to Forward and Backward Directions
3. Two digital pins to read the encoder outputs to get accurate measurements for speed and direction

Vision Subsystem - Requires communication to exchange sensor data structures through serial USB communication. The top-level microcontroller is designed to abstract away the complication of the sensor data and perform path planning and communicate with the main low-level controller subsystem, designed in this signoff, which will execute commands to drive motors and drive actuators. 

The vision system will house all of the sensor for data acquisition (micro and macro location) for the robot and will communicate with the top-level main microcontroller. The top-level main microcontroller will communicate with the low-level main microcontroller via serial USB. The top-level microcontroller will have a dedicated operating system (likely some Linux distribution) and will act as the master where the two low-level microcontrollers, designed in this signoff, will act as the slaves. The USB will allow master and slave to communicate with each other serially with universal asynchronous transmitter receiver (UART) and can be software defined consistantly across master and slave. 

_Total pins needed:_
| Locomotion, Fireworks, and Feeding, Consumption Controller | |
|---|----|
| Power: | 2  |
| Digital: | 12 |
| PWM: | 7  |
| Interrupt: | 2  |
| Total: | 17 |

### Object Sorting and Storage Controller

Object Sorting - belt motor and a motor or pressurized air which will poke the pedestals off of the belt and into a separate area.

| Object Sorting | | | | |
|---|---|---|---|----|
| Motor Driver | Pin Type  | Count | | |
| Speed | PWM | 1 | | |
| Forward Direction  | Digital | 1 | | |
| Backward Direction | Digital | 1 | | |
| Color Sensor | | | | |
| Ground | Power | 1 | | |
| Interrupt | Interrupt | 1 | | |
| SCL | Digital | 1 | | |
| SDA | Digital | 1 | | |
| VDD | Power | 1 | | |
| Vibration Motor | | | | |
| Positive | Power | 1 | | |
| Negative | Power | 1 | | |
| Activation | Digital | 1 | | |
| Linear Actuator | | | | |
| Retract | Digital | 1 | | |
| Extend | Digital | 1 | | |
| | | | Interrupt:  | 1  |
| | | | PWM: | 1  |
| | | | Power: | 4  |
| | | | Digital: | 7  |
| | | | Total Pins: | 13 |

_Interfaces needed:_ 
1. Motor to drive conveyor 
2. Color sensor
3. Vibration motor
4. Linear actuator

Object Storage - 

The pins for the object sorting subsystem are listed below in tabular form. The first motor driver is for the rack and pinion system, and two proximity sensors will be in the silos and will determine when they are full. Finally, the last motor driver inputs will be for the mechanism to open the silos when a statue needs to be dropped off. 

| Object Storage | | | | |
|---|---|---|---|----|
| Servo Controller | | | | |
| Communication | Micro-USB | 0 | | |
| Ground | Power | 1 | | |
| Vin | Power | 1 | | |
| Rx | Digital | 1 | | |
| Tx | Digital | 1 | | |
| Reset | Digital | 1 | | |
| Proximity Sensor | | | | |
| Vin | Power | 2 | | |
| Ground | Power | 2 | | |
| Out | Digital | 2 | | |
| | | | Power: | 6  |
| | | | Digital: | 5  |
| | | | Total Pins: | 11 |

_Interfaces needed:_ 
1. Motor for rack and pinion
2. two proximity sensors
3. some motor for opening the silo

_Total pins needed:_
| Object Storage and Sorting Controller | |
|---|----|
| Power: | 10 |
| Digital: | 12 |
| PWM: | 1  |
| Interrupt: | 1  |
| Total: | 24 |

The Arduino Mega 2560 Rev3 was analyzed for selection as the main low-level controller and the object sorting and storage controller. The board has 54 digital pins, 15 of which can be used as PWM outputs, 16 analog inputs, 4 UARTS, and a USB connection.

The Arduino Mega can integrate ROS, and ROS will definitely be used in this project. ROS libraries will be used for hardware abstraction, low-level device control, and package management.

The Arduino Mega was selected for these two microcontrollers because it has a comfortable cushion for the I/O constraint, and allows us to separate and design the controller system modularly. 

Two microcontrollers are being used so that the design is modular and can be split up in a way that makes sense. The low-level controllers are mostly driving motor controllers with PWM and digital outputs, and those actions are generally not computationally expensive.

The object sorting has a color sensor which will send data at $400\ \frac{kbits}{sec}$, and the Arduino Mega, and the clock of the microcontroller is 16 MHz and with the pre-scale set to 128 by default, this means that the digital pins can be sampled at $150\ \frac{k-bits}{sec}$. The the 128 pre-scale can be changed, so this can be updated to our requirements. Analysis is shown below.

The object storage subsystem has proximity sensors which outputs at 145 Hz, which will be sufficient for our use case of only needing to know when the silos are full. This is not something that needs to be sampled at an extremely high speed. Analysis is shown below. 

## Electronic Schematic

The electronic schematic for the controller subsystem is attached below. It includes the main microcontroller and the interface to each of the subsystems which they require to drive actuators. 



Electronic Schematic Files: [here](https://github.com/nathan-gardner/CapstoneRepo/tree/main/Documentation/Electrical/Schematics/Sources)

Final implementation electrical pin connections on the Arduino Mega are defined in the [source code](/Software/mega2560/mega1/) as C defines. 

## Analysis

The analysis below is used to show why the Arduino Mega microcontroller is going to be be used for the main controller subsystem.

Tables are shown in the constraints section and contain pin count analysis. The pins are one of the major constraints on the design for this subsystem. 

### Color Sensor in Object Sorting

The belt will be moving at $2 \frac{inches}{sec}$

The calculations for the samples per unit distance are below:

$v_{belt} = 2\ \frac{inches}{sec}$

$f_{color\ sensor} = 400\ \frac{ksamples}{sec}$

$f_{arduino} = 150\ \frac{ksamples}{sec}$

$f_{effective} = 75\ \frac{ksamples}{sec}$

$\frac{samples}{inch} = \frac{1\ sec}{2\ inches} \ast \frac{75\ ksamples}{1\ sec} = 37.5\ \frac{ksamples}{sec}$

Calculations for the frequency of objects recieved:

$f_{duck} = \frac{80\ sec}{10\ ducks} = 8 \frac{sec}{duck}$

$f_{pedestal} = \frac{80\ sec}{7\ pedestals} = 11.4 \frac{sec}{pedestals}$

$f_{object} = \frac{80\ sec}{17\ objects} = 4.7 \frac{sec}{object}$

$f_{objects\ received\ on\ belt} = \frac{17\ objects}{80\ sec} =  0.2125\ Hz$

This means that the sample rate of $37.5\ \frac{ksamples}{sec}$ is more than enough for sampling the the color of the objects coming in on the belt. The robot will actually be able to sample a pedestal many times, the calculations for that are below:

$\frac{samples}{L_{pedestal}} = 75\ \frac{ksamples}{sec} \ast \frac{1 sec}{2 inches} \ast \frac{2 inches}{1\ L_{pedestal}}$

Nyquist rate for the color sensor sampling:

$f_{color\ sample} = 2 \ast 2\ Hz = 4\ Hz$

### Proximity Sensor in Object Storage

The silo will need to sampled twice a second, so the actual sampling will be happening at 4 Hz, by Nyquists Theorem.

$f_{proximity\ sample} = 2 \ast 2\ Hz = 4\ Hz$ by Nyquist Theorem.

## Software Analysis - Processing Capabilities and Possible/Probable Software Analysis

Arduino public C++ libraries will be used for these microcontrollers. We will use the built in Arduino PWM functionality in this library to interface with the motors (PWM) and read and write digital pins on the Arduino Mega. Part of the reason why Arduino was chosen as the low level microcontroller is the amount of public libraries available for the devices. Public libraries that will very likely be used in this controller implementation are below.

The **[Core Library Used for Arduino Mega 2560 Rev3](https://github.com/arduino/ArduinoCore-avr)** will be necessary for the low-level microcontrollers in this project, as it is the functions provided by Arduino and in the IDE and is what most peripheral libraries have dependencies on. 

***Some* Specific Software Implementations:**

[Servo](https://github.com/arduino-libraries/Servo/tree/master/src/avr) will be used to drive servo motors and is a public library provided by Arduino. 

[Digital Read](https://github.com/arduino/ArduinoCore-avr/blob/42fa4a1ea1b1b11d1cc0a60298e529d37f9d14bd/cores/arduino/wiring_digital.c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) will read pins and determine if they are logic high or low. 

[Digital Write](https://github.com/arduino/ArduinoCore-avr/blob/42fa4a1ea1b1b11d1cc0a60298e529d37f9d14bd/cores/arduino/wiring_digital.c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) will set output pins as logic high or low.

[Analog Read](https://github.com/arduino/ArduinoCore-avr/blob/42fa4a1ea1b1b11d1cc0a60298e529d37f9d14bd/cores/arduino/wiring_analog.c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) will be used to read PWM coming from the encoder, which will return the speed to the main microcontroller. 

[Analog Write](https://github.com/arduino/ArduinoCore-avr/blob/42fa4a1ea1b1b11d1cc0a60298e529d37f9d14bd/cores/arduino/wiring_analog.c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) will be used to write analog values and to implement PWM functionality to drive DC motors in various subsystems.

[PWM](https://github.com/arduino/ArduinoCore-avr/blob/master/cores/arduino/wiring_analog.c) will be implemented using the analog read and write functions in the public Arduino library.

The Arduino Mega 2560 Rev3's clock runs are 16 MHz using the ATmega2560 microcontroller onboard. The board has 256 KB of flash memory, 8 KB of SRAM, and 4 KB of EEPROM memory. Using the design outlined, be are using a small percentage of the GPIO on the Arduino Mega, because of the modular design. The source code for each project will be compiled so it will be lightweight on flash memory for the Arduino Mega 2560 Rev3. The modular design allows the team to be comfortable that we will not reach computational limitations due to to many peripheral devices connected to a single device. 

The Arduino will not run a dedicated OS, but instead has a basic bootloader that performs hardware and software initialization and then jump to the main method in the code. PlatformIO will likely be used as the IDE for this project because of its extra functionality in importing dependencies and integration into VScode as an extension. PlatformIO has 650 boards available including the Arduino Mega 2560 Rev3 so PlatformIO has been chosen for is versatility. 

## BOM

| Name of Item | Description | Used in which subsystem(s) | Part Number | Manufacturer | Quantity | Price | Total  |
|---|---|---|---|---|---|---|---|
| Arduino Mega 2560 Rev3 | Microcontrollers selected for controller subsystem | Controller | A000067/7630049200067 | Arduino | 2 | 48.4 | 96.8 |
| Jumper Wires ELEGOO 120pcs | Jumper wires to connect board to sensors and motors | Controller | B01EV70C78 | ELEGOO | 1 | 9.99 | 9.99 |
| Total | | | | Total Components | 3 | Total Cost | 106.79 |

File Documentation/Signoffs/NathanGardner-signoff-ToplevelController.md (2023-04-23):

# Top-level Controller Subsystem Signoff

The top-level controller for the robot is the controller that is used as the master for the ROS network on the robot. All other controllers besides the top-level will be Arduino or some other microcontroller, and not have a dedicated full operating system.

## Brief overview of the controller network as a whole

The top-level controller will be connected via USB to the two low-level controllers, which will both be an Arduino Mega 2560. These two controllers where designed in a previous signoff, one of which is dedicated to locomotion, feeding, fireworks, and consumption. The other low level controller is responsible for sorting and storage of the objects around the arena. 

The first low-level controller will have two peripheral Arduino Nano for flipping the switch for the fireworks and the other for controller the actuator that will place the food chips in the correct feeding area. 

It will also send the control signals to the motors for the arena locomotion system. It will send PWM signals to the motor drivers to the control its position in the arena. 

The second microcontroller will be used for the sorting and storage subsystem for the pedestals and ducks for the competition. This will include reading a color sensor for which will in turn actuate a linear actuator that will push pedestals off the conveyor and will allow the ducks to pass, and read a proximity sensor which will initiate a sequence that will drop off a stack of pedestals, a statue, onto the playing field. 

## Function of the Top-level Controller Subsystem

The top-level controller will serve as the master the two aforementioned Arduino Mega controllers, and will serve as the hub for the vision subsystem of the robot. The vision subsystem, which will be a network of sensors, will interface with the top-level controller. The vision subsystem is yet to be designed for this project. 

The top-level controller will host the dedicated OS which is required to orchestrate robot operating system (ROS) connections by serving as the master and providing name registration and lookup for the computation graph. The top-level controller will also have a parameter server which is like a large C struct that will be updated by the nodes when values change in the system. 

Devices, namely the two low level controllers, will host nodes that are dedicated processes for sensors or functions of the robot. This is intended to allow for clean separation of code and to allow for scalability of sensor networks and communication for the robot. 

## Constraints

The top-level controller must have two USB type A ports that will be used to connect the two low-level controllers. The controller must also communicate with the vision sensor network and retrieve data, process that data, and send commands to actuators around the robot, which will perform actions in the arena.

The controller has a size constraint as does the robot. The top-level controller cannot get too hot and cannot require a large fan to cool, because of the power and space constraints. 

In summary, these constraints are as follows:
- Power
- Size
- GPIO
- Computation speed and minimum system specification requirements

## Electrical Schematic



The 40-pin header connection design is represented in the vision sensor network sign off, and not in the top-level controller sign off. The rest of the connections in the top level controller are represented here. 

One Arduino Mega controller ended up being needed for implementation with subsystems that needed to be cut due to ordering issues.  

## Analysis

The top-level controller will need to be analyzed in terms of the constraints: power, size, and GPIO. 

The actual power consumption of a fully equipped Nano running at maximum clock speed sits between 15 - 25 Watts. To power the Nano along with the necessary peripherals through the Micro USB or USB C port, using a 5V adapter that can output 2.5 Amps or higher. If the team uses a 5V DC barrel jack adapter, the outputs must be at least 4 Amps.

The size of Nvidia Jetson Nano Developer Kit 100 x 80 x 29 mm. The team compared this size to the Arduino Mega 2560, which is 53.3 x 101.52. This is a reasonable footprint and the Jetson Nano Dev Kit has mounting holes so that it can be mounted to the robot. 

The total number of GPIO pin headers is 40. The spreadsheet with the GPIO breakdown is below: 

| Type | Count |
|---|---|
| USB 3 | 4 |
| Ethernet | 1 |
| UART | 2 |
| SPI | 2 |
| HDMI Output Port | 1 |
| DisplayPort Connector | 1 |
| I2C | 2 |
| I2S | 1 |
| PWM | 2 |
| AUDIO_MCLK | 1 |
| LCD_TE | 1 |
| CAM_AF_EN | 1 |
| GPIO_PZO | 1 |
| GPIO_PE6 | 1 |
| LCD_BL_PWM | 1 |

The computation speed and minimum system specification requirements are discussed below in the software analysis portion of this document. 

## Software Analysis - Processing Capabilities and Possible/Probable Software Solutions

This section covers using ROS as a communication framework, and not using the SLAM packages which are available within ROS. ROS will be used for hardware abstraction, low-level device control, functionality implementation, process-to-process messaging, and package management. ROS, in the way it will be implemented on the top-level controller, uses a [publish/subscribe](https://en.wikipedia.org/wiki/Publish%E2%80%93subscribe_pattern) communication protocol. 

It has been determined that ROS packages will not be used to produce point maps or to perform localization as it relates to the robots navigation, so ROS is exclusively being used for its hardware abstraction, low-level device control, functionality implementation, and process-to-process messaging libraries. To achieve this, the top-level controller will need to have enough compute/ processing power to perform the tasks required of the master: orchestrating connections (naming and registration services) within the computation graph, and hosting nodes within the computation graph itself. This in itself is not very computationally intensive, and according to the [ROS forums](https://www.instructables.com/Getting-Started-with-ROS-Robotic-Operating-Syste/), requires a dual-core computer clocked at 1.6 GHz and at least 2 GB of RAM. The Nvidia Jetson Nano Developer Kit selected meets these requirements. 

The ROS master will be running on the Nvidia Jetson Nano and ROSSerial will be used to establish ROS topics (connections) between the top-level controller and the low-level controllers. As of creating this sign off, the team has been able to create a ROS master on a personal computer (emulating the top-level controller) and create a ROS node on one of the Arduino Mega 2560. This is a simple demo available [here](https://github.com/nathan-gardner/CapstoneRepo/tree/main/Software/demo/Test_ROSSerial), which established a "chatter" topic and publishes std_msg/Int32 data to the topic which can be read by the emulated top-level controller.

This simple demo was created based on this [article](https://sites.duke.edu/memscapstone/using-rosserial-to-setup-a-ros-node-on-a-teensy/) to demonstrate the viability of the design outlined in this sign-off and for the controller network (top and low-level) as a whole, and to make sure ROS was installed correctly. This method for uploading code to the Arduino uses PlatformIO, which is general purpose for different micro-controllers like Arduino, ESP, STM, etc.. It was determined to be the most versatile option instead of using the ArduinoIDE directly.  

ROS has a large amount of community support and will serve as a useful robotics framework. If ROS is unable to be implemented, we will need to use traditional Arduino programming style and establish a serial connection using PySerial between the top-level controller and the low-level controller. This is what ROSSerial is doing but it has already built the framework to create nodes, establish topics, and to publish and subscribe to those topics.

As an example of this implementation, Nathan wrote a [ROS node](https://github.com/nathan-gardner/CapstoneRepo/blob/main/Software/mega2560/sub_consumption/src/main.cpp) for the consumption subsystem which can control the motor speed remotely from anywhere in the ROS computation graph. This uses message passing outlined above, and is what the team plans on using for the serial communication within the controller network. The code in the ROS node above establishes communication between the top and low level controller through topics, one named /consumption/motorState (published) and the other named /consumption/cmdMotorState (subscribed). /consumption/cmdMotorState can be updated from the top level or any node in the computation graph, and this while invoke the analogWrite function on the Arduino and publish an updated value to the /consumption/motorState topic, which is also visible within the computation graph. 

## BOM

| Name of Item | Description | Used in which subsystem(s) | Part Number | Manufacturer | Quantity | Price | Total  |
|---|---|---|---|---|---|---|---|
| Nvidia Jetson Nano Developer Kit | Top-level controller | Top-level controller | 945-13450-0000-100 | Nvidia | 1 | 149.99 | 149.99 |
| 16 GB or larger UHS-1 microSD card | Storage device with the Jetson Nano (256 GB) | Top-level controller | LMSESXX256G-BNAEU  | Lexar | 1 | 24.99 | 24.99  |
| 5V DC barrel jack power input cable | Standard barrel jack connector | Top-level controller | B07JGR7JJQ | SIOCEN | 1 | 9.99 | 9.99 |
| iClever DK03 Bluetooth Keyboard and Mouse | USB connection with a bluetooth chip | Top-level controller | B08KZXLTM6 | iClever | 1 | 39.99 | 39.99  |
| MYFON Micro-USB Cable | Micro USB Cable | Top-level controller | B098DW7485 | MYFON | 1 |  6.99 |  6.99  |
| Total | | | | Total Components | 4 | Total Cost | 231.95 |

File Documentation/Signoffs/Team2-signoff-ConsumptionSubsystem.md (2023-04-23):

# Consumption Subsystem Signoff -> Delivery Subsystem Signoff (updated 4/19/2023)

## Function of the Subsystem

This subsystem went through a major redesign shortly before the competition to ensure reliability and as many points as possible when competing. Changes implemented are described below. 

The consumption subsystem’s main goal is to pick up any duck and pedestal that is in the predetermined path of the robot. Throughout the competition, the robot will make a complete path through the entire playing field that will be predetermined and designed by the team and come in contact with all of the ducks and pedestals that are present. The robot will need to pick these items up in order to later sort them and place them in their proper locations that are discussed within other subsystems. 

The consumption needed to be repurposed due to a lack of implementation time and to create a more reliable and robust system. The consumption was converted into a delivery system and the direction of the motors were reversed to that the robot could collect items in its path, and then spit them out in the recycling area for points. 

### Function:
- Intake the object via ~~three~~ two rows of spinning shafts with spokes
- ~~Spokes (flexible material held in place with set screws on a D-profile carbon steel shaft) will push objects against the body of the robot and take the captured ducks and pedestals upwards towards the top of the robot with motion from a DC brushed motor~~
- Spokes (flexible material held in place with set screws on a D-profile carbon steel shaft) will push objects out of the robot after they have been collected and the robot is near the recycling area
- Worst case scenario of three ducks analyzed below

## Constraints

The consumption subsystem has a few constraints that it must abide by in order to be successful. The first constraint is that it must have a motor that has a minimum torque of $0.2168\ N \ast m$. The calculations used to find this minimum torque are laid out in the constraints portion of this document. The torque was determined based on the weight of the ducks on the spokes of the intake mechanism as well as the anticipated friction of the spokes pushing the ducks against the body of the robot and the floor. We found the weight of the ducks to be $70.8\ g$ and the friction constant of the rubber duck on the aluminum body of the robot to be $0.64$. The weight of the duck was considered because the weight of the pedestals is much less than that of the duck.

Taking the weight of the ducks into consideration, this places a constraint on the team’s decision of which material to use for the design. TPU will be used to build the spokes for the intake mechanism and use set screws on a D-profile carbon steel shaft to hold the spokes in place. The calculations used to determine these materials are shown below in the analysis portion of the document. The weight of the duck ( $70.8\ g$ ) had to be taken into consideration as well as the rigidity we need for both materials. The ducks weigh much more than the pedestals, so the duck’s weight was used for all calculations. The set screws that hold the spokes in place need to be rigid enough to securely hold all them while supporting multiple ducks in the worst case scenario.  

Assuming all three shafts are lifting a single duck, the maximum weight the motor will need to move would be $212.4\ g$. The acceleration of gravity ( $9.8\ m/s^2$ ), the friction constant of rubber against the aluminum side of the robot ( $0.64$ ), and the weight of the ducks ( $0.0708\ kg$ ) combined was used to find the force perpendicular to the moment arm of the spokes. Once the force needed based on the weight of the duck and the friction on the body of the robot was found, the force, the length of the spokes, and sine of the angle in which the items will be traveling were multiplied to find the torque needed to lift multiple ducks.

The ratio of the torque for each shaft is proportional to the ratio of the diameter of the two wheels either driving or being driven by the belt. The diameter of the driving wheel on the motor is 0.88 inches and the diameter of the three wheels being turned is 1.75 inches. That means the multiplication constant is 1.998. The torque for the three shafts being driven would therefore need to be 1.988 times what our calculations for the needed torque of the motor is, or $0.441 \ast 1.988$, which equals $0.877\ kg \ast cm$. This calculation is in the maximum torsional sheer strength calculation later in this report.

Additionally, the team needs to analyze whether or not the motor will meet the speed needed to pick up the items within the allotted amount of time. As previously mentioned, the motor will need to have a torque of $0.877\ kg \ast cm$. Assuming the motor provides 60 rpm as a worst-case scenario and the ducks are in full contact with the spokes for the entire rotation, the upwards velocity of the ducks would be approximately $11 \frac{ in }{ sec }$. Assuming the ducks need to travel 10 inches to make it to the conveyor belt, the ducks will make it to the top of the robot in 1.1 second. This value displays that even at a worst case, the spokes will be able to intake the objects at the speed necessary.

The next constraint that was considered was fitting the system within the size of the robot. The robot must fit in a 1’x1’x1’ area, so this adds the constraint of fitting each subsystem of this robot within the available space. The size of the consumption subsystem had to be such that the ducks would be accommodated. The duck’s size was considered more so than the pedestal because the duck has much larger measurements than the pedestal. The team’s object consumption design takes up $600\ inch^3$ including the motor. The analysis to find this value is shown below in the team’s 3D model of the system. 

Another constraint is that the robot must pick up all the objects in its path in a specific and constrained amount of time. This is essential to the robot's proper function because the round length is three minutes. Object consumption cannot take a large majority of the time because we need to allow for time to move the ducks to the pond and to activate the fireworks. Two minutes was determined as the maximum possible time that the robot will be allowed to consume objects around the arena and this means that the robot will need to move six inches per second. Two minutes was selected because it is the optimal balance which allows for time to transverse the arena at a reasonable speed ( $6\ \frac{inches}{sec}$ ) and allows for another minute to complete the duck delivery and firework activation. The path the robot will take is below and is total 480 inches long. This was analyzed to determine the amount of items the robot needs to consume in the two minutes. 

The object frequency analysis in the analysis section uses the velocity of the robot's movement and the amount of ducks and pedestals in the arena to perform a rough calculation of the object frequency. These calculations assume that the objects are completely evenly spread across the arena, which is the best approximation given the information we have from the competition explanation, that the objects will be randomly spread around the arena. This will likely not be exactly the case, but we are assuming complete randomness in analysis. 



The maximum shear strength calculations are below and were used in the selection of materials for the construction of the object consumption subsystem. The shear is the strain on a structure caused by pressure when its layers are laterally shifted in relation to each other. The maximum shear strength is of carbon steel is analyzed in the analysis portion below.  

Standard: OSHA Standard 1910.212(a)(1) states that guards are needed around moving parts. The robot’s consumption mechanism will be surrounded by walls on three of the four sides to account for this guard.

Conceptual Design Document: [here](https://github.com/nathan-gardner/CapstoneRepo/blob/main/Reports/Team2_ConceptualDesignandPlanningFinal.pdf)

## Buildable schematic 

Shown below is our buildable schematic design made in SOLIDWORKS. The spokes will rotate and intake any duck or pedestal in the robot’s path. The consumption mechanism will have three rows of spokes that will direct the objects upwards and inwards up a ramped wall to the beginning of the sorting mechanism. The back wall will have the ability to be adjusted within the testing phase in order to ensure that the spokes are close enough to the wall to properly intake each item. The spokes will be made of TPU and the rotating shafts will be made of pvc pipes for prototyping, but carbon steel for the final product. The ramp will be made of some kind of printed plastic for prototypes and aluminum for the final product. All calculations and analysis were done for the final product, not the prototype. All measurements shown on the 3D model are in inches. 

### Electrical Schematic



### Intake Mechanism Back
IntakeMechanismBack

### Intake Mechanism Front
IntakeMechanismFront

### Intake Mechanism Front Angle
IntakeMechanismFrontAngle

### Intake Mechanism Side
IntakeMechanismSide

### Intake Mechanism Side
IntakeMechanismSide2

### Intake Mechanism inside box of robot (guards in place according to safety standard)

CAD Files for Object Consumption Mechanism: [here](https://github.com/nathan-gardner/CapstoneRepo/tree/main/Documentation/3D%20Models/ConsumptionSystem/Intake_Assembly_11-9-222)

## Analysis

### Motor Torque



The DC brushed motor chosen is part number #4805 from Pololu. The motor is considered high power and runs off of $6\ V$. The torque needed for the motor to supply in the worst case is $0.877\ kg \ast cm$. This torque value was found using a Simulink simulation shown below. The target rpm we want to run the motor at is $120\ rpm$, motor #4805 produces a torque of about $9.1\ kg \ast cm$, which is more than enough for the worst case scenario. The power needed for $120\ rpm$ is about $4\ W$ and will draw close to $2.75\ A$. The power subsystem will be designed to deliver adequate power to the motor used in this subsystem. The motor's gear ratio is 46.85:1 and uses a metal spur gear box internal to the motor. 





The simulation above depicts the friction of the spokes against the body of the robot in the feedback loops on the left side of the model. The three forces from the ducks are added and the torque required to push those ducks is calulated and graphed on the oscilloscope as the output. The equation we used for the torque is $\tau = F \ast r \ast sin(\theta)$.

The safety factor for motor selection was two times the needed torque based on simulations. 

Motor torque Simulink Model: [here](https://github.com/nathan-gardner/CapstoneRepo/tree/main/Software/matlab-sim/ConsumptionSystem)

### Maximum Torsional Shear Strength 

### Torque ratio calculation

$\frac{ \tau_{shaft} }{ \tau_{drive} } = \frac{r_{shaft}}{r_{drive}}$

$\tau_{shaft} = \frac{r_{shaft} \ast \tau_{drive}}{r_{drive}}$

$\tau_{shaft} = 1.988 \ast \tau_{drive}$

$\tau_{shaft} = 0.877\ kg \ast cm$

Since the motor we selected is rated for up to $9.1 kg \ast cm$, it will meet the needs of the team since it exceeds the maximum rating of the motor. 

### Torsional Shear Strength Calculation

$\tau_{max}=\frac{16T}{\pi d^{3}}$

$T_{shaft} = 0.877\ kg \ast cm = 0.086\ N \ast m$
(torque at the top of the power peak considering gear ratio internal to the motor)

$d = 0.00635\ m$
(shaft diameter)

$= 1,710,600\ Pa$

$= 1.71\ MPa$

Normal carbon steel ranges between $260 - 500\ MPa$. Thus, the material chosen for the design will be sufficient. 

### Object Frequency Analysis

Stated in the contraints section, we are assuming the robot will transverse a 480 inch path in 120 seconds, and of that time, 80 seconds will be used for actual robot forward motion. Calculations for time per object consumed is below:

$f_{duck} = \frac{80\ sec}{10\ ducks} = 8 \frac{sec}{duck}$

$f_{pedestal} = \frac{80\ sec}{7\ pedestals} = 11.4 \frac{sec}{pedestals}$

$f_{object} = \frac{80\ sec}{17\ objects} = 4.7 \frac{sec}{object}$

### Motor Speed Intake Analysis

Assuming a worst case scenario of 60 rpm and each item staying in full contact with the spokes for the entire ride up the intake, the following calculations were made.

$\omega = 60 rpm = 2 \ast \pi \frac{ rad }{ sec }$

$v = r \ast \omega = 1.75 \ast 2 \ast \pi = 10.996 \frac{ in }{ sec }$

Since we need to pick up items at a rate of $4.7 \frac{sec}{object}$, this expected and absolute worst case scenario will still be enough to push the items up at a rate in which the robot will be able to collect all the items. 

## BOM

The bill of materials for the consumption mechanism is below. This includes all parts that are needed for design and manufacture of the robot. 

| Name of Item | Description | Used in which subsystem(s) | Part Number | Manufacturer | Quantity | Price | Total  |
|---|---|---|---|---|---|---|---|
| D Profile Shaft  | D-Profile rotary shaft, D-profile ends, 1045 Carbon steel, 3/8'' Diameter, 12'' Long | Consumption | 3832T1 | McMaster-Carr | 3 | 11.67 | 35.01  |
| Bushing/Bearing  | Ball bearing, Shielded, Trade Number R6-2Z for 3/8'' Shaft diameter | Consumption | 60355K45 | McMaster-Carr | 6 | 6.25 | 37.5 |
| Shaft Collar | Set Screw Shaft Collar for 3/8" Diameter, Black-Oxide 1215 Carbon Steel | Consumption | 9414T8 | McMaster-Carr | 6 | 1.75 | 10.5 |
| Shaft Pulley | Corrosion-Resistant Timing Belt Pulley, XL, 3/8" Maximum Width, Hub, 2 Flange, 1.75" OD, 3/8" Shaft | Consumption | 1277N28 | McMaster-Carr | 3 | 16.65 | 49.95  |
| Motor Pulley | Corrosion-Resistant Timing Belt Pulley, XL Series, 3/8" Maximum Belt Width, with Hub, 2 Flanges, 7/8" OD | Consumption | 1277N41 | McMaster-Carr | 1 | 10.2 | 10.2 |
| Timing Belt | XL Series Timing Belt, Trade No. 210xL025 | Consumption | 6484K219 | McMaster-Carr | 1 | 6.97 | 6.97 |
| Motor | 47:1 Metal gearmotor 25Dx67L mm HP 6V with 48 CPR Encoder | Consumption | 4805 | Pololu | 1 | 48.95 | 48.95  |
| Motor Controller | TB9051FTG Single Brushed DC Motor Driver Carrier | Consumption | 2997 | Pololu | 1 | 11.95 | 11.95  |
| Washer Pack | 316 Stainless Steel Washer for 3/8" Screw Size, 0.406" ID, 0.75" OD | Consumption | 90107A127 | McMaster-Carr | 1 | 9.5 | 9.5 |
| Corner Bracket | Corner Machine Bracket, Finish-Your-Own, 6061 Aluminum, 1" x 1" x 1-1/4" | Consumption | 2313N36 | McMaster-Carr | 1 | 7.24 | 7.24 |
| Side Profile | Fabricated by 3D printer | Consumption | | | 2 | 0 | 0 |
| Ramp Element | Fabricated by 3D printer | Consumption | | | 1 | 0 | 0 |
| TPU Spoke | Fabricated by 3D printer | Consumption | | | 12 | 0 | 0 |
| Forward Ejection | Fabricated by 3D printer | Consumption | | | 1 | 0 | 0 |
| Motor Mount | Fabricated by 3D printer | Consumption | | | 1 | 0 | 0 |
| Total | | | | Total Components | 41 | Total Cost | 227.77 |

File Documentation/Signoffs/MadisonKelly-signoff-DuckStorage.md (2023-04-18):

# Duck Storage and Delivery Subsystem Signoff

This subsystem was not implemented in the competition due to changes made with 
consumption.

## Function of the Subsystem

Throughout each round of the competition, the robot will need to intake up to 17 items, 10 of which are ducks, via the consumption subsystem. These ducks that are collected will need to be ~~sorted and~~ stored until they are dropped off at their proper location on the playing board. The storage subsystem’s main function is to take in the ducks from the sorting subsystem, store them in their respective location, and drop them off at their proper location on the playing board. The ducks will be held in a corral connected to the back of the robot. When the predetermined path is completed, the robot will go to the duck pond and eject the corral via a rack and pinion mechanism.

### Function:

- Store the ducks in a bottomless corral that rolls behind the robot
- Have a locking mechanism that will ensure the corral is not lost when being rolled behind the robot
- Rack and pinion mechanism for rolling back the corral at the beginning of the competition as well as when the ducks are to be delivered.
- Drop the ducks and corral off in the duck pond via a drawer and lock-style solenoid mechanism
- Worst case scenario of all ten ducks at a time is analyzed below

## Constraints

- To abide by the 1 cubic foot size constraint, the trailer will extend from the back of the robot via a rack and pinion mechanism. 
- The ducks are approximately 3 inches x 3 inches x 3.5 inches, so the corral will need to be a sufficient size to hold all ten ducks. The ducks can sit on top of each other, so the corral shown in the buildable schematic will be sufficient to hold all ten ducks.
- The servo motor selected for the corral design should have at least 16.83 $kg \ast cm$ of torque.
- The distance that needs to be travelled for the initial roll back of the corral at the beginning of each round is 9 inches which will require 9 rotations or 3240&deg;. For the final drop off, it will need to travel 1 inch which will require 1 rotation or 360&deg;.
- The duck trailer will need to have a locking mechanism to ensure that it does not roll off of the rack when the robot is in motion. To address this, the team plans to add two lock-style solenoids and lock the trailer in place to stop any unwanted motion. 
- The pinion gear will need to have some way to "mesh" with the the rack that is mounted on the side of the trailer. In order to prevent it from coming off the rack, the team will 3D print an enclosure to ensure the pinion gear stays on the rack. The 3D model below shows this feature in more detail.
- The omni-wheel on the back of the trailer should be attached such that the gap between the bottom of the back wall of the trailer and the playing field is not large enough that a duck or part of a duck could get jammed in the space and cause extra resistance on the robot's locomotion subsystem.
- This system will affect the path taken along the playing field as well as the time constraints, analyzed below. 
- The final constraint comes from the ethical consideration of a pinching hazard near the rack and pinion and lock-style solenoid system. We will design the system so that the rack and pinion are not directly exposed to the open, which would create a pinching hazard. 

## Electrical Schematic

The electrical schematic for the object storage subsystem is shown below. Please note that the circuit components will be implemented via a solderable breadboard. The circuit layout is as specified by the manufacturer's datasheet.



The link to the Schematic Document is found here.

## Analysis

### Size Calculations for Duck Corral

#### Duck Trailer
$Duck\ Volume = 3 \ast 3 \ast 3.5 = 31.5 in^{3}$

$Duck\ Volume_{Total} = 31.5 \ast 10 = 315 in^{3}$

$Corral\ Volume = 6 \ast 11.25 \ 9 = 607.5 in^{3}$
  
Corral Volume >> Duck Volume. Therefore, the corral can hold the ducks.

### Torque Ratio Calculations

To find the Torque needed for the Servo Motor for the Rack and Pinion the following calculations were completed. Using 90&deg; as a worst case scenario.

$Total\ Mass = m_{ducks} + m_{trailer} = 0.708 + 1.04 = 1.748$

$F = m \ast 9.81 \ast 0.76 = 1.748 \ast 9.81 \ast 0.76 = 13.03 N$

$\tau = F \ast r \ast sin(\theta) = 13.03 \ast 0.0127 \ast sin(90&deg;) = 1.65 N \ast m$

$\tau = 1.65 N \ast m = 16.83 kg \ast cm$

Assuming a worst case velocity of spinning out the entire corral in 4 seconds, the velocity would need to be $2.5 \frac{in}{sec}$

$\omega = \frac{v}{r} = \frac{2.5}{05} = 5 \frac{rad}{sec} = 47.75 rpm$

We know that the servo motor that was selected can supply more than enough rpm, so it should be able to spin the corral out at the speed necessary.

### Rotation Calculation for Corral 

#### Initial Roll Back

$C = \pi \ast d = \pi \ast 1$

$Rotations = \frac{ distance }{ C } = \frac{ 9 }{ 1 } = 9$

$Degrees = rotations \ast 360 = 9 \ast 360 = 3240 &deg;$

#### Final Delivery

$C = \pi \ast d = \pi \ast 1$

$Rotations = \frac{ distance }{ C } = \frac{ 1 }{ 1 } = 1$

$Degrees = rotations \ast 360 = 1 \ast 360 = 360 &deg;$

### Lock-Style Solenoid Analysis

The lock is normally active, so it will not require power while in the locked state. It is designed for a 1-10 second activation time.

Keeping in mind that the duck trailer can be fully ejected in 4 seconds, this solenoid will be more than adequate for allowing the trailer to roll past when necessary.
  
#### Omni-Wheel Height
 
The onmi-wheel is adjustable, so the team can decide how far or how close to the ground the trailer should be. The duck's beak is approximately 0.25 inches.

In order to ensure the duck's beak does not get caught under the trailer, the omni-wheel must be placed at a height such that the trailer sides are no more than 0.25 inches off the ground. Due to the adjustable nature of the omni-wheel, this will be possible.

### Affect on Navigation

While the extra weight and friction was analyzed in the locomotion subsystem, the actual impact this will have on navigation will be analyzed within this one.

The navigation path will have to account for a robot with a length of 18 inches rather than 12 inches which would be the case without the trailer. In order to be as conservative as possible, we planned for the maximum robot length for our path that the robot will take. The playing field is 4 feet by 8 feet, there will be no objects closer than 2 inches to the walls, and our robot is now 18 inches long. This constrains our path when making turns. The consumption subsystem which is mounted to the front of the robot must also be facing the front when traversing the playing field. While making turns will be more difficult with the trailer, it will still be possible. Images of the path are shown below.



















Notice that the robot never goes more than 37.75 inches from the side wall. Therefore, this path will be the one the robot takes for each turn. According to the pre-determined path, the robot will only have to make four turns when doing the initial traversal of the playing field. 

### Timing

The affect this subsystem has on navigation will also affect the amount of time the competition rounds will take. According to the pre-determined path, the robot will only have to make four turns when doing the initial traversal of the playing field. This turning mechanism will add an additional 34.5 inches to our path per turn. 

$4\ turns \ast 34.5\ in = 138\ inches$

$480\ total\ path\ length + 138\ inches = 618\ in$

According to the locomotion subsystem's calculations, the robot can travel at up to 0.2023 $\frac{m}{s}$. Assuming the robot can go this full speed on straight-aways, the following calculations are performed.

$480\ in = 12.192\ m = \frac{12.192}{0.2023} = 60.3\ sec$

Assuming the turns will take 5 seconds each,

$60.3\ sec + 4 \ast 5\ sec = 80.3\ sec$

Therefore, the robot can still traverse the entire playing field in less than half the time (3 minutes). This leaves an additional minute and 40 seconds to complete all the other tasks. In addition to this, locomotion signoff calculates an 84.66\% margin of safety. This means that the motors only are using 15.34\% of their torque capacity, so there will be plenty of extra speed as needed.

## Buildable Schematic









You can find the 3D models for all Components here.

Below are images showing how all of the subsystems, including Duck Storage Subsystem will fit into the robot.

Top view



Rear Side view 1



Rear Side view 2



Rear view



Front corner



## BOM

| Name of Item | Description | Used in which subsystem(s) | Part Number | Manufacturer | Quantity | Price | Total |
|---|---|---|---|---|---|---|---|
| Solenoid Mount | Print | Duck Storage | N/A | N/A | 1 | 0 | 0 |
| Corner Bracket | Print | Duck Storage | N/A | N/A | 4 | 0 | 0 |
| Steel Ball Transfer | Steel Ball Transfer(21 mm Height) | Duck Storage | 1619-001-001 | Servo City | 1 | 2.99 | 2.99  |
| Lock-Style Solenoids | 12 V-DC | Duck Storage | 1512 | Adafruit | 2 | 14.95 | 29.9  |
| Aluminum Sheet | Sides and Backing for Duck Corral - Multipurpose 6061 Aluminum Sheet, 1/8'' thick, 6'' x 12'' | Duck Storage | 6061 | McMaster Carr | 3 | 24.28 | 72.84 |
| Rack | 14-1/2 Degree Pressure Angle Gear Rack, 32 Pitch (1ft) Nylon Plastic | Duck Storage | 57655K62 | McMaster Carr | 2 | 8.94 | 17.88 |
| Servo-Mounted Pinion | 32P, 32 Tooth, 25T 3F Spline Servo Mount Gear (Acetyl) | Duck Storage | RSA32-2FS-32 | McMaster Carr | 2 | 3.94 | 7.88  |
| Servo Motor | 2000 Series Dual Mode Servo | Duck Storage | 2000-0025-0002 | Servo City | 1 | 31.99 | 31.99 |
| Servo Motor Controller | 3102 Series Dual Mode Servo Programmer | Duck Storage | 3102-0001-0001 | Servo City | 2 | 9.99 | 19.98 |
| TIP102 Transistors | Darlington Transistors in order to have the ability to switch on and off the solenoid to lock the trailer | Duck Storage | 976 | Adafruit | 1 | 2.5 | 2.5 |
| Servo Controller | Micro Maestro 6-Channel USB Servo Controller | Duck Storage, Pedestal Storage, and Feeding | 1350 | Pololu | 1 | 39.95 | 39.95 |
| Total | | | | Total Components | 21 | Total Cost | 225.91 |

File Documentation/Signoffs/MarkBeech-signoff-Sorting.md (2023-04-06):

# **Sorting Subsystem** - Not Implemented

Due to shipping issues, this subsystem was cut.

## **Function of The Subsystem** 
- Take ducks and pedestals from the comsumption susbsytem to their proper storage locations via a conveyor belt and flipper.
- Actively sort pedestals while passively sorting ducks. 
- Objects will be passed from the consumption subsystem to the sorting subsystem. The sorting subsystem will then send the ducks to the duck storage and delivery subsystem while sending the pedestals to the pedestal storage and delivery subsystem.
- The motor driver for the DC motor will be controlled via the low-level controller subsystem.
- The driver for the servo motor is a part of the duck storage and delivery subsystem which will be controlled by the low-level controller subsystem.

## **Constraints**
### **Size:**
- The sorting subsystem must be designed to be space efficient due to the robot having a size constraint of 1 cubic foot. The consumption subsystem takes up $5 \ in$ of depth, so the sorting subsystem must be no longer than $7 \ in$ deep. The sorting subsystem must be at the top of the robot due to the consumption susbsytem feeding objects out to the top of the robot. There must be sufficient space for a pedestal silo and funnel under the sorting subsystem. The silo will be $5.5 \ in$ tall. The funnel has been designed to be $2.75 \ in$ tall, thus making the funnel and silo together $8.25 \ in$ tall. The conveyor will be above the funnel with a height of $1 \ in$. The flipper will be no greater than $1.5 \ in$ tall. This makes the total height of the sorting subsystem $10.75 \ in$. This number was found by adding the height of the funnel and silo with the height of the conveyor and maximum height of the flipper.
### **Conveyor:**
- The size of ducks will constrain the width of the conveyor belt. The belt must have a width wider than the duck's width of 3.5 $\ in$.
- The conveyor belt must effectively move ducks and pedestals at $2\ in/s$ and support the weight of at least three ducks ( $F_{ducks} = 2.08152\  N$ ).
- The length of the conveyor must be no more than $7 \ in$ to make room for the consumption subsystem (the consumption subsystem is $5\ in$ deep into the robot).
### **Flipper:**
- Flipper must be long enough to reach across the whole conveyor belt width ( $3.5 \ in$ )
- The flipper must be tall enough to push a pedestal and not cause spin or disturb other objects. The chosen width is $1.5 \ in$.
- The servo and flipper must provide enough force to move the pedestals ( $F_{flipper} \gt 1.5572 \ N$ ).
### **Sensor:**
- Color sensor and flipper must be at least $1.238\  in$ from each other to ensure the sensor has adequate time to detect the color of the object that passes by. More distance may be required to accomodate the speed of the microcontroller that will control the servo for the flipper. See the color sensor section under the analysis section for more details.
- The color sensor must be able to distinguish between pink, yellow, red, green, and white.
- Color sensor must work well with the Arduino architecture.
### **Socioeconomic:**
- Some parts were chosen to be 3D-printed instead of purchased in order to save cost.

## **Buildable Schematic**

### **CAD Model for the subsystem:**



















### **Electrical Schematics:**



## **Analysis**
### **Conveyor Belt**:

#### **Belt length**:
Conveyor length $L = 7in$ (Chosen)

$C$ is the center to center distance $C = 7 - 2(0.5) = 6\ in$ of the drive pulley $D$ (chosen to be 1 in)

Belt Length ( $l$ )

$l = D\pi + 2C = 1\pi +2(6) = 15.1416\ in$

$\ $
#### **Normal and Frictional Forces**:
Worst case scenario assumed to be 3 ducks on the conveyor at once:

Force Calculations:

Normal Force of one duck:

$F_{Nduck} =(0.0708\ kg)(9.8\ m/s) = 0.6938\  N$

Force of three ducks on the conveyor belt:

 $F_{ducks} =3(0.0708\ kg)(9.8\ m/s) = 2.08152\  N$

Weight of three Ducks:

$W_{ducks} = (0.225)(2.08152) = 0.4683\ lbs$

Friction Force of Duck:

$F_{fduck} = kF_{Nduck} = (1.15)(0.0708\ kg)(9.8\ m/s) = 0.7979 \ N$

Normal Force of one pedestal:

$F_{Nped}=(0.0206\ kg)(9.8\ m/s) = 0.20188$

Friction Force of Pedestal:

$F_{fped} = kF_{Nped} = (1.15)0.20188= 0.2322 \ N$

$\ $

### **Torque needed**:

Efficiency: $\eta$ Assumed to be 50%

Assuming worst case of three ducks:

$F = F_{fduck} + 3m_{duck}(g)(sin(\theta) + kcos(\theta)$

$F = 0.7979 + 0.0708(9.8)(sin(0) + 1.15cos(0)) = 1.4917\ N$

$T_{L} = \frac{FD}{2\eta } =\frac{(1.4917)(0.0254)}{2(0.5)} = 0.03789 \ N \ast m$

$\ $
#### **Conveyor Speed:**
Chosen speed to be at least $2\  in/s = 10\ ft/min$

Speed of conveyor $s$

$s = D(RPM)(0.2618)(1.021)$

$\rightarrow  RPM = \frac{s}{(0.2618)(1.021)(D)} = \frac{10}{(0.2618)(1.021)(1)} = 37.5\  RPM$

$\ $
#### **Power Required:**

Approximate weight of rubber = $24.94\ g/cm^3 = 0.05498\ lbs/cm^3$

Belt Dimensions in inches = 15.1416 in X 3.75 in X 0.0625 in 

Belt Dimensions in cm = 38.46 cm X 9.525 cm X 0.15875 cm

Belt Volume $=(38.46)(9.525)(0.15875) = 58.155\ cm^3$

Weight of Belt $W_{belt} = (0.05498)(58.155) = 3.1974 \ lbs $

Friction coefficient of rubber: $k = 1.15$

$P = \frac{ks(W_{ducks}+W_{Belt})(745.7)}{33000}$

$P = \frac{(1.15)(5)(0.4683+3.1974)(745.7)}{33000} = 0.5855 \ W$

$\ $
#### **Conveyor Motor Requirements Summarized:**
$Torque > 0.03789 N \ast m$ or $3.86\ kg \ast mm$

$RPM = 37.5$

Below is the torque curve for the motor chosen from Pololu.



Therefore, the motor chosen meets all specifications.

According to the datasheet for the motor driver, it will be able to supply the necessary voltage and current values (6 V, 250 mA). This is the same motor driver used for the consumption motor which requires double the current compared to this subsystem

$\ $
### **Flipper:**
The flipper consists of a servo motor connected to a 3D printed plastic "pinball" flipper.

weight of ABS $1.03 \frac{g}{cm^3}$

Assuming the plastic flipper is rectangular:

 $3.5in$ x $1in$ x $1.5in$ = $5.25 \ in^3$ = $86.03209 \ cm^3$

 $W_{block} = (1.03 \frac{g}{cm^3})(86.03209 \ cm^3) = 88.6130527 \ g = 0.0886 \ kg$

$(0.0886 \ kg)(9.81) = 0.869 N$

Force needed to push block attached to the servo:

$F_{fplastic}= 0.869 \ N$

Force needed to push the pedestal on rubber:

$F_{fped}= 0.2322 \ N$

Total force needed to be applied by the servo:

$F_{flipper}= 0.2322 \ N + 1.325 \ N = 1.5572 \ N$

The flipper must apply more force than this in order to push the pedestal into the funnel.

$\tau = F_{flipper}(r)(sin(\theta)) = 1.5572(0.0889)(sin(90)) = 0.13 \ N \ast m$

$\ $
### **Color Sensor:**

Electrical Specifications:

$V_{DD} = 3\ V$ 

$I_{DD} = 235\ \mu A \ \ (Active)$ 

$I_{DD} = 65\ \mu A \ \ (Wait)$ 

$I_{DD} = 2.5\ \mu A \ \ (Sleep)$ 

The above voltages and currents will be provided by one of the Arduino Megas from the low-level controller subsystem.

$\ $

Speed:

Clock Frequency: $\ \ 0-400kHz$



Above is the state machine representation for the sensor circuit showing the times each of the states will take. For the majority of the time, the sensor will be in the states idle, RGCB ADC and RGCB INIT after the startup. Detection will take a maximum of 616.4 ms.

Pedestals have a diameter of $2 \ in$ and the conveyor moves at $2 \ \frac{in}{s}$ which means that one point of the pedestal will be in front of the sensor for 1 second which allows for plenty of time for the sensor to detect the color of the object as detection takes a maximum of 0.614 ms.

Minimum flipper distance from sensor $=(0.6164\ s)(2\ in/s) = 1.2328 \ in$

Flipper distance will be $1.5\ in$ for simplicity.

$\ $

## **BOM**

| Name of Item | Description | Used in which subsystem(s) | Part Number | Manufacturer | Quantity | Price | Total  |
| --- | --- | --- | --- | --- | --- | --- | --- |
| Color Sensor | RGB Color Snesor with IR filter and White LED | Sorting | TCS34725 | Adafruit | 1  | $7.95 | 7.95 |
| Servo Motor | Analog Servo | Sorting | 2818 | Fitech | 1  |  $5.25 |  $5.25 |
| Motor | 99:1 Metal Gearmotor 25Dx69L mm LP 6V with 48 CPR Encoder | Sorting | 4827 | Pololu | 1  | $45.95 | 45.95  |
| Funnel | 3d printed | Sorting | N/A | N/A | 1  | | 0 |
| Flipper | 3d printed | Sorting | N/A | N/A | 1  | | 0 |
| Rubber Belt | Rubber-Cal Heavy Black Conveyor Belt - Rubber Sheet - .30(2Ply) Thick x 10"" Width x 4"" Length - Black (3 Pack) | Sorting | N/A | Rubber-cal | 1  | $56 | 55.65  |
| Rollers | 3d printed | Sorting | N/A | N/A | 2  | | 0 |
| DC Motor Controller | TB9051FTG Single Brushed DC Motor Driver Carrier | Sorting | 2997 | Pololu | 1  | $11.95 | 11.95  |
| Motor Mount | Pololu 25D mm Metal Gearmotor Bracket Pair | Sorting | 2676 | Pololu | 1  | $7.95 | 7.95 |
| Total | | | | Total Components | 10 | Total Cost | 134.70 |

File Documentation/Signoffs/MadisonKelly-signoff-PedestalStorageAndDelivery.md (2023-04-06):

# Pedestal Storage and Delivery - Not Implemented

Due to shipping issues with the sorting subsystem, this subsystem was not able to be implemented.

## Function of the Subsystem
Throughout each round of the competition, the robot will need to intake up to seven pedestals. Once the pedestals are collected, they’ll need to be sorted and stored until it is the appropriate time to drop them off. The team plans to collect three pedestals before placing them wherever the robot may be upon the collection of the third pedestal. After that, it will place one or two stacks of two depending on whether or not all pedestals were collected. 
This subsystem’s main function is to ensure that the pedestals have a place to be stored as well as a method of delivery. The pedestals will be in the correct orientation from the sorting subsystem, and the silo in which each pedestal will stay will include two proximity sensors in order to detect the number of pedestals in the silo at all times. As previously stated, once three pedestals are detected in the robot, they will be dropped off by opening the silo and driving the robot away from the statue. For the next two iterations, the silo will open when there are only two pedestals since there are only seven pedestals total. The complexity of the subsystem is decreased as opposed to the duck delivery because the pedestals can be placed anywhere on the playing field. 
- Store all collected pedestals in the silos in the correct orientation	
- “Full” sensor will detect when there are two or three pedestals present 
- Drop the statues off whenever they are collected (first a statue that is three pedestals tall and after that, a statue that is two pedestals tall)
- Worst case scenario of three pedestals at a time is analyzed below

## Constraints
- The 1’x1’x1’ size constraint for the robot causes the design to need to be as area-effective as possible. There will only be one silo that is 5.5 in (height) x 2.25 in (width) x 2.25 inches (length).

- There will be two proximity sensors placed in the silo to send an interrupt signal back to the controller to stop the main path transversal and allow time for the silo to open and the robot to move away to drop off the pedestals. 

- The servo motor selected for the silo extension and pedestal drop off should be able to withstand the weight of at most three pedestals and the weight of the silo itself. In the worst case, the motor will have 0.0618 kg (the weight of three pedestals) + 0.06287 kg (the weight of the silo). It will need at least 3.495 $kg \ast cm$ of torque to function.

- Calculations for the rotation angle of the servo motor are in the analysis section below. The silo will need to open widde enough to let the statue fit through which will require .318 rotations or 115 degrees. The silo will remain open until enough time has elapsed that it can close again without trapping the statue within the silo.

- Another constraint that needs to be considered for this subsystem is the silo placement. The team’s plan is to drop off the pedestals upon collection. The silo will be on the side of the robot. The door will open and the robot will drive directly sideways away from the statue, leaving it behind. 

## Electrical Schematic
The electrical schematic is shown below.



## Buildable Schematic





Shown with sensors inside.

thumbnail_proxsensors
thumbnail_sideangle_proxsensors
thumbnail_top_proxsensors

Below is the rough layout of the chassis showing the major subsystems and their placement within the robot. This subsystem is in the block labeled "pedestals".

chassis

Below are images showing how all of the subsystems, including the Pedestal Storage and Delivery subsystem will fit into the robot.

Top view



Rear Side view 1



Rear Side view 2



Rear view



Front corner



Chassis Subsystem Fit CAD model files available [here](https://github.com/nathan-gardner/CapstoneRepo/tree/main/Documentation/3D%20Models/Chassis/Chassis_Fit).

## Analysis
### Size Calculations for Pedestal Silo

$Pedestal\ Volume = \pi \ast r^{2} \ast h = \pi \ast 1^{2} \ast 1.8 = 5.65 in^{3}$

$Pedestal\ Volume_{Total} = 5.65 \ast 3 = 16.96 in^{3}$

$Silo\ Volume = 5.5 \ast 2.25 \ast 2.25 = 27.84 in^{3}$

Silo Volume > Pedestal Volume. The diameter of the pedestals are 2 inches and the width and length of the silo is 2.25 inches. Therefore, the silos can hold the pedestals.

### Distance From Sensors

Because of the nature of what the team is wanting from the distance sensor, it must be such that it will not detect the walls of the silo, but will detect the presence of a pedestal.

#### Pedestal Not Present

$Silo\ Wall\ Distance\ from\ sensor = 2.25 in$

$Max\ sensor\ range = 5cm = 1.9685 in$

Since 2.25 in > 1.97 in, the sensor will not detect the walls of the silo itself. 

#### Pedestal Present

$D_{max} = L_{silo} - D_{pedestal} = 2.25in - 2in = 0.25 in = 0.635 cm$

The max distance calculated is less than the maximum distance the sensor can detect which is 5 cm. The distance between the wall of the silo and the sensor is more than its maximum range. Therefore, the sensors will be able to detect the pedestals when they enter the silo and will not detect the walls of the silo when there is no pedestal present. According to the manufacturer, the sensor will output a "low" signal when there is an object present and a "high" signal otherwise. The sensor will only detect if there is an object within range, so if there is not, it will output a defined signal showing that there is no object present.

### Weight Calculations

$W_{pedestals} = 20.6 g \ast 3 = 0.0618 kg$

$W_{silo} = 5.5 \ast 2.5 \ast 0.25 \ast% density of TPU = $3.4375 \ast 0.0448 = 0.154 lbs = 0.06287 kg$

$W_{total} = 0.0618 + 0.06287 = 0.12467 kg$

### Torque Calculations

$F = m \ast a = 0.12467 \ast 9.81 = 1.223 N$

$\tau = F \ast r \ast sin(\theta) = 1.223 \ast 0.07258 m \ast sin(90) = 0.0888 N \ast m = 0.9055$

The servo motor chosen is able to supply 3.5 $kg \ast cm$ of torque. Therefore, the servo will be sufficient for the design.

### Rotation Calculation for Statue Delivery

$C = \pi \ast d = \pi \ast 2 = 6.28$

$Rotations = \frac{ 2 }{ 12.56 } = 0.318$

$Degrees = rotations \ast 360 = 0.318 \ast 360 = 114.64&deg;$

This rotation angle is well within the servo's capabilities. 

### How Long will the Silo need to remain open?

To determine how long the silo will need to remain open to allow the statues to be left untouched, the speed of the robot must be determined. The robot will be moving at or greater than $0.0677 \frac{m}{s}$ after opening the silo and releasing the pedestal.

$0.0677 \frac{m}{s} = 2.665 \frac{in}{s}$

If the pedestal is two inches in diameter, the silo will need to remain open for no less than one second to allow the statue to exit the robot and remain intact and unharmed by the edges of the silo.

## BOM
| Name of Item | Description | Used in which subsystem(s) | Part Number | Manufacturer | Quantity | Price | Total |
|---|---|---|---|---|---|---|---|
| Proximity Sensor | Pololu Digital Sensor 5cm | Pedestal Storage and Delivery | 4050 | Pololu | 2 | 12.95 | 25.9  |
| Servo Motor | FEEFETCH Standard Servo FT1117M | Pedestal Storage and Delivery | 3423 | Pololu | 1 | 9.95 | 9.95  |
| Silo | Silo to hold pedestals, 3D Printed | Pedestal Storage and Delivery | N/A | N/A | 1 | 0 | 0 |
| Servo Mount | 3D Printed | Pedestal Storage and Delivery | N/A | N/A | 1 | 0 | 0 |
| Servo Motor Controller | Micro Maestro 6-channel USB Servo Controller | Duck Storage, Pedestal Storage, and Delivery and Feeding | 1350 | Pololu | 1 | 39.95 | 39.95 |
| Total | | | | Total Components | 6 | Total Cost | 75.8  |

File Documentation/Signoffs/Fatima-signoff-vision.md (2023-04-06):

# Vision Sensor Network Subsystem Signoff - Not Implemented

The vision subsystem was cut due to not recieving sensors. 

# Function of the subsystem

The vision subsystem for this robot includes the sensor network that will be used for localization within the arena. The path will be preprogrammed into the robot as a large block of conditionals which will access sensor data from the vision subsystem.

The team chose the Adafruit VL53L0X Time of Flight Micro-LIDAR Distance Sensor for distance measurements in the arena and the RGB Color Sensor with IR filter for color sensing within the robot for active sorting and in order to find landmarks within the arena. 

The subsystem uses the top-level controller for processing sensor data, reading data more rapidly, and publishing the data to a ROS topic to communicate to the rest of the nodes within the computation graph. Nodes will be created for data acquisitions from the sensors, and will be decoupled from the logic that is making the robot follow its path through the arena. The path locomotion logic will be another node in the network which will subscribe to the data stream created by the sensor nodes, and produce command data for the low-level controller to create at a set interval which will activate the motors to follows the set command encoded in that data stream.

The team chose to use the TCS34725 Color Sensor to detect the duck pond location, which is also used within the design for the sorting subsystem for distinguishing between ducks and pedestals with are going through the bots conveyor belt system. 

## Function

The vision subsystem is a sensor network that will allow the robot to determine its position in the arena. This is done by finding the distance to the nearest walls, and also using a color sensor pointed towards the ground to detect the feeding areas and the duck pond in the middle of the arena. 

-	Large and small scale measurements are needed to detect position from distance and color
-	The sensors will communicate with top level microcontroller, the color sensor needs to be capable of distinguishing needed colors in the arena: blue, red, green, pink, and yellow. 
    - This communication between the top-level controller to the rest of the controller network will be within the ROS computation graph, so that the sensor acquisition and production can be decoupled from the actual navigation logic. They would be able to run entirely independent from one another but will only work if they are both running at the same time. 

# Constraints

The closest to the wall the robot will need to localize, or project a LIDAR towards a wall to find it general position in the arena, is near the wall at the duck pond. This will be $9"\ -\ \frac{width\ of\ robot}{2}=9" - 5.625" = 3.375" = 8.573\ cm$. This can be assumed because no objects will be within $2"$ of the wall, or $5.08\ cm$. The farthest from the wall that the robot will need to localize within the arena with the ToF LIDAR sensor is the length of the arena minus half the width of the robot, which is $48" - \frac{11.25"}{2} = 42.375" = 107.63\ cm$. This maximum distance will be when the robot is in the center of the arena long ways, for example, in the duck pond. The robot time of flight LIDAR sensors need to have be be able to measure between $5.08\ -\ 107.63\ cm$ with an accuracy of $+/-\ 0.707"$ or $+/-\ 1.8 cm$. This is within the distance range of $5\ -\ 120\ cm$ for the absolute distance, which is specified within the LIDAR sensor data sheet. The accuracy requirement ( $+/-\ 1.8 cm$ ) is analyzed below in the analysis section of this sign off. 

The robot must distinguish between different colors on the color spectrum, specifically the difference between black ( `0x000000` ) and blue ( `0x2876BB` ), so that the robot can localize over the duck pond to deliver the duck trailer precisely. These color values were taking from color sampling the image in the competition rules.
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

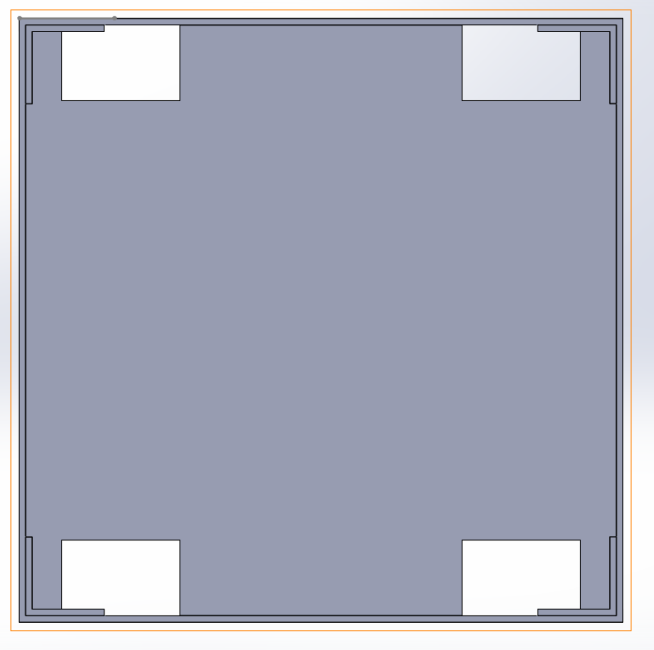
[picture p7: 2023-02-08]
Documentation/Images/FireWorks/ChassisTopView.png

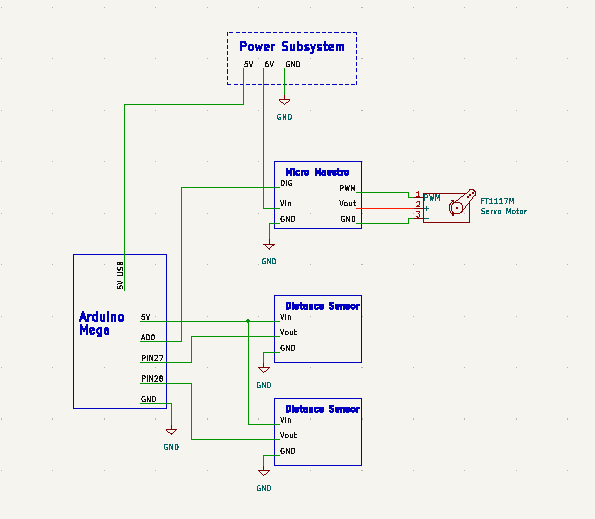
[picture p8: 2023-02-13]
Documentation/Images/updated schematic.png

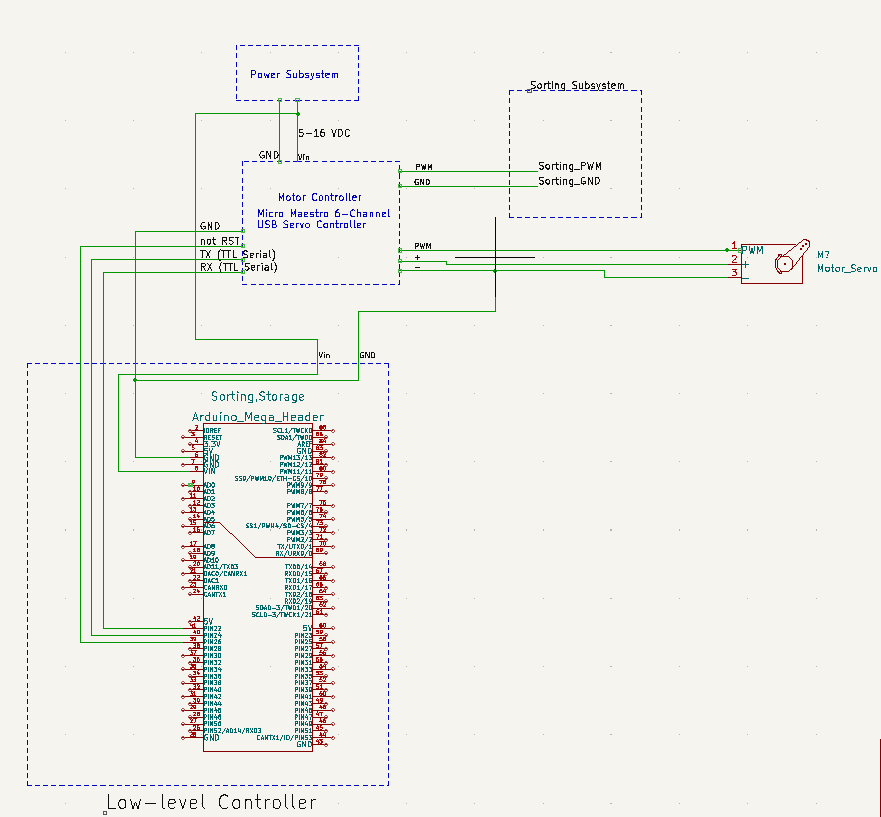
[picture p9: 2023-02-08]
Documentation/Images/Schematic.PNG

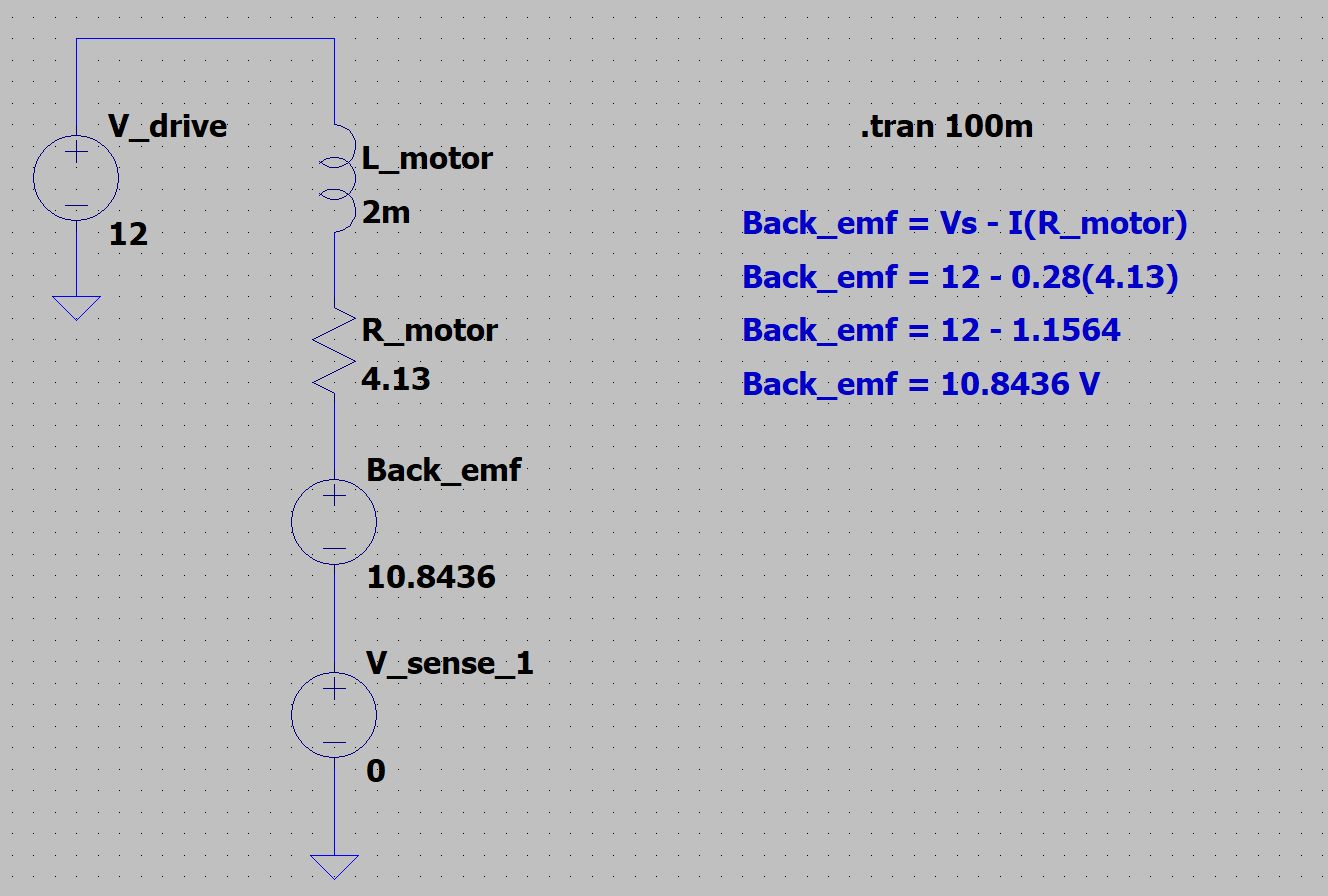
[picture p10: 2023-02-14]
Documentation/Images/PowerSubsystem/Locomotion_motor.png

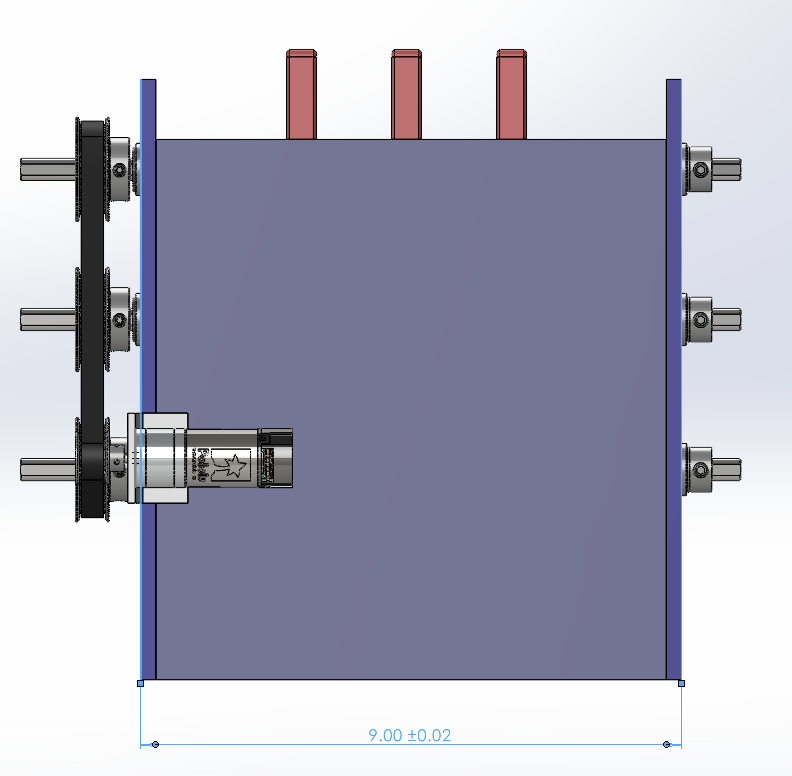
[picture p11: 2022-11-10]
Documentation/Images/ConsumptionSystem/IntakeMechanismBack.png

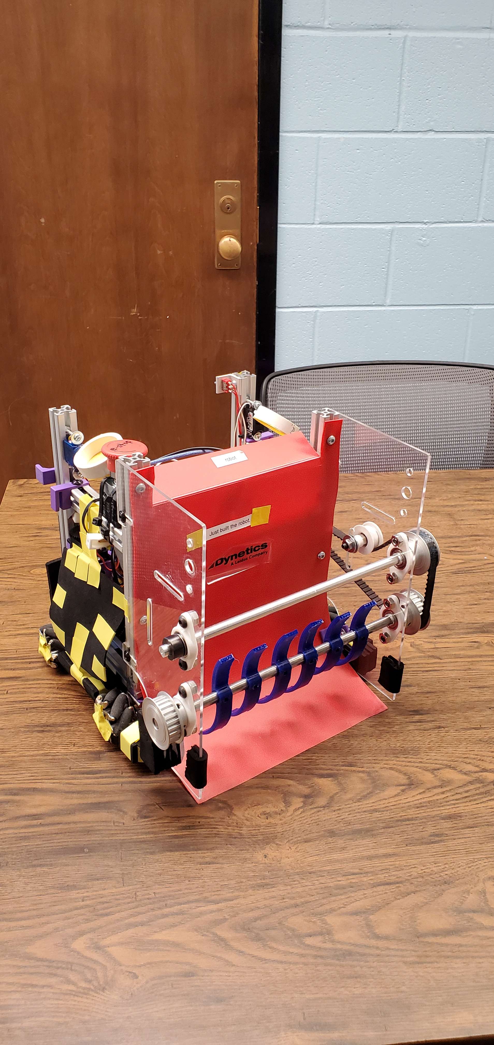
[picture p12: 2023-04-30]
Documentation/Images/robot/robotfront1.jpg

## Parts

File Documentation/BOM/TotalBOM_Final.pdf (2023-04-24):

Name of Item | Description | Used in which subsystem(s) | Part Number | Manufacturer | Quantity | Price | Total | Used?
Rechargeable 12 V Battery | 12 V/6000 mAH Lithium Ion Battery Pack | Power | YB1206000-USB | TalentCell | 1 | $39.99 | $39.99 | TRUE
Buck Converters | | Power | LM2596 | ATNSINC | 3 | $15.69 | $47.07 | TRUE
E-Stop Button | | Power | HB2-BS544 | MXUTEUK | 1 | $10.99 | $10.99 | TRUE
3 A Fuses | 3A 250V Fuses (pack of 20) | Power | F3AL250V | BOJACK | 2 | $5.99 | $11.98 | TRUE
1N5822 Diode | Power | 1N5822 | Ximimark | 1 | $7.29 | $7.29 | 1
0.1 uF Capacitors | Power | 0.1 uF | E-Projects | 1 | $5.99 | $5.99 | 1
1 uF Capacitor | Power | TAP105K050SCS | KYOCERA AVX | 1 | $0.82 | $0.82 | 1
330 uF Capacitors | | Power | 330 uF | changhe | 1 | $18.98 | $18.98 | 1
33 uH inductors | | Power | 33 uH | uxcell | 1 | $8.49 | $8.49 | 1
DC-DC Converter | DC DC Converter 12 V 120 W | Power | 209-JCK4012S12 | XP Power | 1 | $71.50 | $71.50 | 1
TIP 102 Transistor | Darlington Transistors NPN Power Darlington | Power | 511-TIP102 | STMicroelectronics | 4 | $0.99 | $3.96 | 1
Power Distribution Bus | Solid Brass | Power | 737 | Adafruit | 5 | $1.95 | $9.75 | 1
Steel Ball Transfer | Steel Ball Transfer(21 mm Height) | Duck Storage | 1619-001-001 | Servo City | 1 | $2.99 | $2.99 | 1
Lock-Style Solenoids | 12 V-DC | Duck Storage | 1512 | Adafruit | 2 | $14.95 | $29.90 | 1
Aluminum Sheet | | Duck Storage | 6061 | McMaster Carr | 3 | $24.28 | $72.84 | 1
Rack | | Duck Storage | 57655K62 | McMaster Carr | 2 | $8.94 | $17.88 | 1
Servo-Mounted Pinion | | Duck Storage | RSA32-2FS-32 | McMaster Carr | 2 | $3.94 | $7.88 | TRUE
Servo Motor | 2000 Series Dual Mode Servo | Duck Storage | 2000-0025-0002 | Servo City | 1 | $31.99 | $31.99 | TRUE
Servo Motor Controller | 3102 Series Dual Mode Servo Programmer | Duck Storage | 3102-0001-0001 | Servo City | 2 | $9.99 | $19.98 | TRUE
TIP102 Transistors | | Duck Storage | 976 | Adafruit | 1 | $2.50 | $2.50 | TRUE
Servo Controller | Micro Maestro 6-Channel USB Servo Controller | | 1350 | Pololu | 1 | $39.95 | $39.95 | TRUE
Servo Motor | FEETECH FS90 Micro Servo | Feeding | 2818 | Pololu | 1 | $5.25 | $5.25 | 1
Proximity Sensor | Pololu Digital Sensor 5cm | Pedestal Storage and Delivery | 4050 | Pololu | 2 | $12.95 | $25.90 | 1
Servo Motor | FEEFETCH Mini Servo FT1117M | Pedestal Storage and Delivery | 3423 | Pololu | 1 | $9.95 | $9.95 | 1
Color Sensor | RGB Color Sensor with IR filter and White LED | Sorting | TCS34725 | Adafruit | 1 | $7.95 | $7.95 | 0
Motor | | Sorting | 4827 | Pololu | 1 | $45.95 | $45.95 | FALSE
Belt | | Sorting | N/A | NABOWAN | 1 | $20.99 | $20.99 | FALSE
DC Motor Controller | | Sorting | 2997 | Pololu | 1 | $11.95 | $11.95 | FALSE
Servo Motor | FEETECH FS90 Micro Servo | Sorting | 2818 | Pololu | 1 | $5.25 | 5.25 | FALSE
Motor Mount | Pololu 25D mm Metal Gearmotor Bracket Pair | Sorting | 2676 | Pololu | 1 | $7.95 | $7.95 | FALSE
Arduino Mega 2560 Rev3 | Microcontrollers | Low-Level Controller | A000067/7630049200067 | Arduino | 2 | $48.40 | $96.80 | TRUE
Jumper Wires ELEGOO | 120 pcs | Low-Level Controller | B01EV70C78 | ELEGOO | 1 | $9.99 | $9.99 | TRUE
Servo Motor | FEETECH FS90 Micro Servo | Feeding | 2818 | Pololu | 1 | $5.25 | $5.25 | TRUE
12V DC Motor | 12V DC Motor | Locomotion | 4865 | Pololu | 4 | $45.95 | $183.80 | TRUE
Motor Mount | DC Motor Mount (pack of 2) | Locomotion | 2676 | Pololu | 2 | $7.95 | $15.90 | TRUE
Mecanum Wheels | 48 mm Mecanum Wheels (pack of 4) | Locomotion | 14209 | Nexus Robot | 1 | $41.84 | $41.84 | TRUE
Wheel Coupling | 4 mm Brass Wheel Coupling | Locomotion | 18077 | Nexus Robot | 4 | $2.34 | $9.36 | TRUE
DC Motor Controller | DC Motor Driver (pack of 4) | Locomotion | L298N | ST | 1 | $11.39 | $11.39 | TRUE
| Top - Level Controller | Top-Level Controller | 945-13450-0000-100 | Nvidia | 1 | $149.99 | $149.99 | TRUE
microSD Card | Storage device with Jetson Nano (256 GB) | Top-Level Controller | LMSESXX256G-BNAEU | Lexar | 1 | $24.99 | $24.99 | TRUE
| Standard Barrel Jack Connector | Top-Level Controller | B07JGR7JJQ | SIOCEN | 1 | $9.99 | $9.99 | TRUE
| | Top-Level Controller | B08KZXLTM6 | iClever | 1 | $39.99 | $39.99 | TRUE
Micro USB Cable | MYFON Micro-USB Cable | Top-Level Controller | B098DW7485 | MYFON | 1 | $6.99 | $6.99 | TRUE
Color Sensor | RGB Color Sensor with IR filter and White LED | Vision | TCS34725 | Adafruit | 2 | $7.95 | $15.90 | FALSE
Distance Sensor | | Vision | VL53L0X | Adafruit | 8 | $14.95 | $119.60 | FALSE
Resistors | | Vision | EFR-W0D50-A:MF | EDGELEC | 1 | $5.99 | $5.99 | FALSE
D Profile Shaft | | Consumption | 3832T1 | McMaster-Carr | 3 | $11.67 | $35.01 | TRUE
Bushing/Bearing | | Consumption | 60355K45 | McMaster-Carr | 6 | $6.25 | $37.50 | TRUE
Shaft Collar | | Consumption | 9414T8 | McMaster-Carr | 6 | $1.75 | $10.50 | TRUE
Shaft Pulley | Consumption | 1277N28 | McMaster-Carr | 3 | $16.65 | $49.95 | TRUE
Motor Pulley | | Consumption | 1277N41 | McMaster-Carr | 1 | $10.20 | $10.20 | TRUE
Timing Belt | XL Series Timing Belt, Trade No. 210xL025 | Consumption | 6484K219 | McMaster-Carr | 1 | $6.97 | $6.97 | TRUE
Motor | | Consumption | 4805 | Pololu | 1 | $48.95 | $48.95 | TRUE
Motor Controller | | Consumption | 2997 | Pololu | 1 | $11.95 | $11.95 | TRUE
Washer Pack | | Consumption | 90107A127 | McMaster-Carr | 1 | $9.50 | $9.50 | TRUE
Corner Bracket | | Consumption | 2313N36 | McMaster-Carr | 1 | $7.24 | $7.24 | TRUE
Total | Total Components | 103 Total Cost | $1,579.40

DC-DC Adjustable Buck Converters 3-40V to 1.5-35V
Self-Locking Emergency Stop Button 2 NC Red Mushroom 660 V 10 A

Ximimark 100Pcs 1N5822 Schottky Diode 3A 40V DO-201AD (DO-27) Barrier Rectifier Diode
for Household Appliances

E-Projects - 0.1uF Ceramic Disc Capacitor - 50 Volts (25 Pieces)

1 µF Conformal Coated Tantalum Capacitors 50 V Radial 8Ohm
Capacitor 4.7UF 6.8UF 10UF 15UF 22UF 47UF 100UF 220UF 330UF 470UF 680UF 1500UF Electrolytic Capacitors Kit 6.3V 10V 16V 25V 35V 50V 100V 400V,295Pcs
uxcell 50Pcs 0510 Color Ring Inductor 33uH 1W Axial RF Choke Coil Inductor

Sides and Backing for Duck Corral -Multipurpose 6061 Aluminum Sheet, 1/8'' thick, 6'' x 12''
14-1/2 Degree Pressure Angle Gear Rack, 32 Pitch (1ft) Nylon Plastic
32P, 32 Tooth, 25T 3F Spline Servo Mount Gear (Acetyl)

Darlington Transistors in order to have the ability to switch on and off the solenoid to lock the trailer

Duck Storage, Pedestal Storage, Sorting, and Feeding

99:1 Metal Gearmotor 25Dx69L mm LP 6V CPR
Encoder

NABOWAN Solid Rubber Sheets,Strips,Rolls 1/16" (.062") Thick x 4" Wide x 120" Long, Thin
Neoprene Rubber, Perfect for DIY Gasket Material, Sealing, Liner, Shield, Padding, Mat TB9051FTG Single Brushed DC Motor Driver
Carrier

Nvidia Jetson Nano Developer Kit

5V DC barrel jack power input cable

Bluetooth keyboard and

mouse

iClever DK03 USB connection with a bluetooth
chip

Time of Flight Micro-LIDAR Distance Sensor
Breakout
EDGELEC 100 pcs 4.7K ohm Resistor 1/2w (0.5Watt) +1% Tol

D-Profile rotary shaft, D-profile ends, 1045 Carbon steel, 3/8'' Diameter, 12'' Long Ball bearing, Shielded, Trade Number R6-2Z for 3/8'' Shaft diameter
Set Screw Shaft Collar for 3/8" Diameter, Black-Oxide 1215 Carbon Steel

Corrosion-Resistant Timing Belt Pulley, XL, 3/8" Maximum Width, Hub, 2 Flange, 1.75" OD, 3/8" Shaft

Corrosion-Resistant Timing Belt Pulley, XL Series, 3/8" Maximum Belt Width, with Hub, 2 Flanges, 7/8" OD

47:1 Metal gearmotor 25Dx67L mm HP 6V with 48 CPR Encoder
TB9051FTG Single Brushed DC Motor Driver
Carrier
316 Stainless Steel Washer for 3/8" Screw Size, 0.406" ID, 0.75" OD
Corner Machine Bracket, Finish-Your-Own, 6061 Aluminum, 1" x 1" x 1-1/4"

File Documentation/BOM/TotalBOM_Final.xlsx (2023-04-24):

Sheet: Sheet1
Name of Item | Description | Used in which subsystem(s) | Part Number | Manufacturer | Quantity | Price | Total | Used?
Rechargeable 12 V Battery | 12 V/6000 mAH Lithium Ion Battery Pack | Power | YB1206000-USB | TalentCell | 1 | $39.99 | $39.99 | TRUE
Buck Converters | DC-DC Adjustable Buck Converters 3-40V to 1.5-35V | Power | LM2596 | ATNSINC | 3 | $15.69 | $47.07 | TRUE
E-Stop Button | Self-Locking Emergency Stop Button 2 NC Red Mushroom 660 V 10 A | Power | HB2-BS544 | MXUTEUK | 1 | $10.99 | $10.99 | TRUE
3 A Fuses | 3A 250V Fuses (pack of 20) | Power | F3AL250V | BOJACK | 2 | $5.99 | $11.98 | TRUE
1N5822 Diode | Ximimark 100Pcs 1N5822 Schottky Diode 3A 40V DO-201AD (DO-27) Barrier Rectifier Diode for Household Appliances | Power | 1N5822 | Ximimark | 1 | $7.29 | $7.29 | TRUE
0.1 uF Capacitors | E-Projects - 0.1uF Ceramic Disc Capacitor - 50 Volts (25 Pieces) | Power | 0.1 uF | E-Projects | 1 | $5.99 | $5.99 | TRUE
1 uF Capacitor | 1 µF Conformal Coated Tantalum Capacitors 50 V Radial 8Ohm | Power | TAP105K050SCS | KYOCERA AVX | 1 | $0.82 | $0.82 | TRUE
330 uF Capacitors | Capacitor 4.7UF 6.8UF 10UF 15UF 22UF 47UF 100UF 220UF 330UF 470UF 680UF 1500UF Electrolytic Capacitors Kit 6.3V 10V 16V 25V 35V 50V 100V 400V,295Pcs | Power | 330 uF | changhe | 1 | $18.98 | $18.98 | TRUE
33 uH inductors | uxcell 50Pcs 0510 Color Ring Inductor 33uH 1W Axial RF Choke Coil Inductor | Power | 33 uH | uxcell | 1 | $8.49 | $8.49 | TRUE
DC-DC Converter | DC DC Converter 12 V 120 W | Power | 209-JCK4012S12 | XP Power | 1 | $71.50 | $71.50 | TRUE
TIP 102 Transistor | Darlington Transistors NPN Power Darlington | Power | 511-TIP102 | STMicroelectronics | 4 | $0.99 | $3.96 | TRUE
Power Distribution Bus | Solid Brass | Power | 737 | Adafruit | 5 | $1.95 | $9.75 | TRUE
Steel Ball Transfer | Steel Ball Transfer(21 mm Height) | Duck Storage | 1619-001-001 | Servo City | 1 | $2.99 | $2.99 | TRUE
Lock-Style Solenoids | 12 V-DC | Duck Storage | 1512 | Adafruit | 2 | $14.95 | $29.90 | TRUE
Aluminum Sheet | Sides and Backing for Duck Corral - Multipurpose 6061 Aluminum Sheet, 1/8'' thick, 6'' x 12'' | Duck Storage | 6061 | McMaster Carr | 3 | $24.28 | $72.84 | TRUE
Rack | 14-1/2 Degree Pressure Angle Gear Rack, 32 Pitch (1ft) Nylon Plastic | Duck Storage | 57655K62 | McMaster Carr | 2 | $8.94 | $17.88 | TRUE
Servo-Mounted Pinion | 32P, 32 Tooth, 25T 3F Spline Servo Mount Gear (Acetyl) | Duck Storage | RSA32-2FS-32 | McMaster Carr | 2 | $3.94 | $7.88 | TRUE
Servo Motor | 2000 Series Dual Mode Servo | Duck Storage | 2000-0025-0002 | Servo City | 1 | $31.99 | $31.99 | TRUE
Servo Motor Controller | 3102 Series Dual Mode Servo Programmer | Duck Storage | 3102-0001-0001 | Servo City | 2 | $9.99 | $19.98 | TRUE
TIP102 Transistors | Darlington Transistors in order to have the ability to switch on and off the solenoid to lock the trailer | Duck Storage | 976 | Adafruit | 1 | $2.50 | $2.50 | TRUE
Servo Controller | Micro Maestro 6-Channel USB Servo Controller | Duck Storage, Pedestal Storage, Sorting, and Feeding | 1350 | Pololu | 1 | $39.95 | $39.95 | TRUE
Servo Motor | FEETECH FS90 Micro Servo | Feeding | 2818 | Pololu | 1 | $5.25 | $5.25 | 1
Proximity Sensor | Pololu Digital Sensor 5cm | Pedestal Storage and Delivery | 4050 | Pololu | 2 | $12.95 | $25.90 | 1
Servo Motor | FEEFETCH Mini Servo FT1117M | Pedestal Storage and Delivery | 3423 | Pololu | 1 | $9.95 | $9.95 | 1
Color Sensor | RGB Color Sensor with IR filter and White LED | Sorting | TCS34725 | Adafruit | 1 | $7.95 | $7.95 | 0
Motor | 99:1 Metal Gearmotor 25Dx69L mm LP 6V CPR Encoder | Sorting | 4827 | Pololu | 1 | $45.95 | $45.95 | FALSE
Belt | NABOWAN Solid Rubber Sheets,Strips,Rolls 1/16" (.062") Thick x 4" Wide x 120" Long, Thin Neoprene Rubber, Perfect for DIY Gasket Material, Sealing, Liner, Shield, Padding, Mat | Sorting | N/A | NABOWAN | 1 | $20.99 | $20.99 | FALSE
DC Motor Controller | TB9051FTG Single Brushed DC Motor Driver Carrier | Sorting | 2997 | Pololu | 1 | $11.95 | $11.95 | FALSE
Servo Motor | FEETECH FS90 Micro Servo | Sorting | 2818 | Pololu | 1 | $5.25 | 5.25 | FALSE
Motor Mount | Pololu 25D mm Metal Gearmotor Bracket Pair | Sorting | 2676 | Pololu | 1 | $7.95 | $7.95 | FALSE
Arduino Mega 2560 Rev3 | Microcontrollers | Low-Level Controller | A000067/7630049200067 | Arduino | 2 | $48.40 | $96.80 | TRUE
Jumper Wires ELEGOO | 120 pcs | Low-Level Controller | B01EV70C78 | ELEGOO | 1 | $9.99 | $9.99 | TRUE
Servo Motor | FEETECH FS90 Micro Servo | Feeding | 2818 | Pololu | 1 | $5.25 | $5.25 | TRUE
12V DC Motor | 12V DC Motor | Locomotion | 4865 | Pololu | 4 | $45.95 | $183.80 | TRUE
Motor Mount | DC Motor Mount (pack of 2) | Locomotion | 2676 | Pololu | 2 | $7.95 | $15.90 | TRUE
Mecanum Wheels | 48 mm Mecanum Wheels (pack of 4) | Locomotion | 14209 | Nexus Robot | 1 | $41.84 | $41.84 | TRUE
Wheel Coupling | 4 mm Brass Wheel Coupling | Locomotion | 18077 | Nexus Robot | 4 | $2.34 | $9.36 | TRUE
DC Motor Controller | DC Motor Driver (pack of 4) | Locomotion | L298N | ST | 1 | $11.39 | $11.39 | TRUE
Nvidia Jetson Nano Developer Kit | Top - Level Controller | Top-Level Controller | 945-13450-0000-100 | Nvidia | 1 | $149.99 | $149.99 | TRUE
microSD Card | Storage device with Jetson Nano (256 GB) | Top-Level Controller | LMSESXX256G-BNAEU | Lexar | 1 | $24.99 | $24.99 | TRUE
5V DC barrel jack power input cable | Standard Barrel Jack Connector | Top-Level Controller | B07JGR7JJQ | SIOCEN | 1 | $9.99 | $9.99 | TRUE
Bluetooth keyboard and mouse | iClever DK03 USB connection with a bluetooth chip | Top-Level Controller | B08KZXLTM6 | iClever | 1 | $39.99 | $39.99 | TRUE
Micro USB Cable | MYFON Micro-USB Cable | Top-Level Controller | B098DW7485 | MYFON | 1 | $6.99 | $6.99 | TRUE
Color Sensor | RGB Color Sensor with IR filter and White LED | Vision | TCS34725 | Adafruit | 2 | $7.95 | $15.90 | FALSE
Distance Sensor | Time of Flight Micro-LIDAR Distance Sensor Breakout | Vision | VL53L0X | Adafruit | 8 | $14.95 | $119.60 | FALSE
Resistors | EDGELEC 100 pcs 4.7K ohm Resistor 1/2w (0.5Watt) +1% Tol | Vision | EFR-W0D50-A:MF | EDGELEC | 1 | $5.99 | $5.99 | FALSE
D Profile Shaft | D-Profile rotary shaft, D-profile ends, 1045 Carbon steel, 3/8'' Diameter, 12'' Long | Consumption | 3832T1 | McMaster-Carr | 3 | $11.67 | $35.01 | TRUE
Bushing/Bearing | Ball bearing, Shielded, Trade Number R6-2Z for 3/8'' Shaft diameter | Consumption | 60355K45 | McMaster-Carr | 6 | $6.25 | $37.50 | TRUE
Shaft Collar | Set Screw Shaft Collar for 3/8" Diameter, Black-Oxide 1215 Carbon Steel | Consumption | 9414T8 | McMaster-Carr | 6 | $1.75 | $10.50 | TRUE
Shaft Pulley | Corrosion-Resistant Timing Belt Pulley, XL, 3/8" Maximum Width, Hub, 2 Flange, 1.75" OD, 3/8" Shaft | Consumption | 1277N28 | McMaster-Carr | 3 | $16.65 | $49.95 | TRUE
Motor Pulley | Corrosion-Resistant Timing Belt Pulley, XL Series, 3/8" Maximum Belt Width, with Hub, 2 Flanges, 7/8" OD | Consumption | 1277N41 | McMaster-Carr | 1 | $10.20 | $10.20 | TRUE
Timing Belt | XL Series Timing Belt, Trade No. 210xL025 | Consumption | 6484K219 | McMaster-Carr | 1 | $6.97 | $6.97 | TRUE
Motor | 47:1 Metal gearmotor 25Dx67L mm HP 6V with 48 CPR Encoder | Consumption | 4805 | Pololu | 1 | $48.95 | $48.95 | TRUE
Motor Controller | TB9051FTG Single Brushed DC Motor Driver Carrier | Consumption | 2997 | Pololu | 1 | $11.95 | $11.95 | TRUE
Washer Pack | 316 Stainless Steel Washer for 3/8" Screw Size, 0.406" ID, 0.75" OD | Consumption | 90107A127 | McMaster-Carr | 1 | $9.50 | $9.50 | TRUE
Corner Bracket | Corner Machine Bracket, Finish-Your-Own, 6061 Aluminum, 1" x 1" x 1-1/4" | Consumption | 2313N36 | McMaster-Carr | 1 | $7.24 | $7.24 | TRUE
Total |  |  |  | Total Components | 103 | Total Cost | $1579.40

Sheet: Sheet2
 |  |  |  | Mechanical Contributions
Full BOM |  | Full BOM (Parts Received) |  | Consumption | 34.9
Power | $236.81 | Power | $236.81 | Arena Supply online and Lowe’s | 269.28
Duck Storage | $185.96 | Duck Storage | $185.96 | Chassis | 753.78
Duck Storage, Pedestal Storage, Sorting, and Feeding | $39.95 | Duck Storage, Pedestal Storage, Sorting, and Feeding | $39.95 | Intake | 43.76
Feeding | $10.50 | Feeding | $10.50 | Duck Storage | 8.97
Pedestal Storage and Delivery | $35.85 | Pedestal Storage and Delivery | $0.00
Sorting | $100.04 | Sorting | $0.00
Low-Level Controller | $106.79 | Low-Level Controller | $106.79
Locomotion | $262.29 | Locomotion | $262.29 | Misc | 126.96
Top-level Controller | $231.95 | Top-level Controller | $231.95
Vision | $141.49 | Vision | $0.00 | Total | 1237.65
Consumption | $227.77 | Consumption | $227.77
Total Cost | $1579.40 | Total Cost (Parts Received) | $1302.02
Full BOM |  | Full BOM (Parts Received)
Power | $236.81 | Power | $236.81
Duck Storage | $185.96 | Duck Storage | $185.96
Duck Storage, Pedestal Storage, Sorting, and Feeding | $48.92 | Duck Storage, Pedestal Storage, Sorting, and Feeding | $48.92
Feeding | $10.50 | Feeding | $10.50
Pedestal Storage and Delivery | $35.85 | Pedestal Storage and Delivery | $0.00
Sorting | $100.04 | Sorting | $0.00
Low-Level Controller | $106.79 | Low-Level Controller | $106.79
Locomotion | $262.29 | Locomotion | $262.29
Top-level Controller | $231.95 | Top-level Controller | $231.95
Vision | $141.49 | Vision | $0.00
Consumption | $306.43 | Consumption | $306.43
Chassis | $753.78 | Chassis | $753.78
Arena Build | $269.28 | Arena Build | $269.28
Miscellaneous | $126.96 | Miscellaneous | $126.96
Total Cost | $2690.09 | Total Cost (Parts Received) | $2412.71

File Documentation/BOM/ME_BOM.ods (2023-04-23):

PART NAME | Quantity | Part NUMBER | SPECIFICATION | Price | SOURCING | LINK
Timing Belt A | 1 | 6484K221 | XL Series Timing Belt, Trade No. 110xL037 (11") | 8.17 | McMaster Carr | LINK (https://www.mcmaster.com/drive-belts/xl-series-timing-belts-8/width~3-8-1/)
Timing Belt B | 1 | 6484K227 | XL Series Timing Belt, Trade No. 210xL025 (17") | 9.54 | McMaster Carr | LINK (https://www.mcmaster.com/drive-belts/xl-series-timing-belts-8/width~3-8-1/)
 |  |  | Total | 17.71
IEEE Mehcanical Part Order 3/30/23
NAME BRIEF | PART NAME | PART # | QTY | UNIT PRICE | TOTAL | SOURCE | Source Link
17.6" Timing Belt | Timing Belt, XL Series, Trade Number 176xL037, 3/8" Wide | 6484K837 | 1 | 10.22 | 10.22 | Mc Master | LINK (https://www.mcmaster.com/catalog/129/1318/6484K837)
 |  |  |  | TOTAL: | 10.22
IEEE Mehcanical Part Order 3/22/23
COMPETITION GAME ELEMENTS
NAME BRIEF | PART NAME | PART # | QTY | UNIT PRICE | TOTAL | SOURCE | Source Link
Feeding Chips | Fun Express Stackable Counting Chips - 600 Pieces | N/A | 1 | 27.93 | 27.93 | AMAZON | LINK (https://www.amazon.com/Fun-Express-59-3086-Stackable/dp/B005HPXAFA)
Yellow Ducks | Classic Yellow Rubber Ducky by Schylling | N/A | 9 | 7.86 | 70.74 | AMAZON | LINK (https://www.amazon.com/Classic-Yellow-Rubber-Ducky-Schylling/dp/B000K21D4K)
Pink Duck | DUCKY CITY 3" Pink Ribbon Rubber Duck | N/A | 1 | 7.50 | 7.50 | AMAZON | LINK (https://www.amazon.com/gp/product/B08LHKRCDZ/ref=ppx_yo_dt_b_asin_title_o07_s00?ie=UTF8&th=1)
MECHANICAL COMPONENTS
Acrylic sheets | Clear Scratch- and UV-Resistant Cast Acrylic Sheet, 12" x 12" x 1/8" | 8560K191 | 3 | 8.46 | 25.38 | McMaster | LINK (https://www.mcmaster.com/catalog/129/4052/8560K191)
8020 Attachments | T-Slotted Framing, End-Feed Nut with Flanged Head, M5 Thread Size (4pk) | 5537T454 | 10 | 3.24 | 32.40 | McMaster | LINK (https://www.mcmaster.com/products/extrusions/t-slotted-framing-fasteners-4/rail-height~1/)
3mm screws | Alloy Steel Low-Profile Socket Head Screw, Hex Drive, M3 x 0.5 mm Thread, 14 mm Long (25pk) | 93070A071 | 1 | 8.12 | 8.12 | McMaster | LINK (https://www.mcmaster.com/catalog/129/3502/93070A067?s=3mm+screws)
5mm screws | Alloy Steel Low-Profile Socket Head Screw, Hex Drive, M5 x 0.8 mm Thread, 8 mm Long (25pk) | 93070A120 | 1 | 7.35 | 7.35 | McMaster | LINK (https://www.mcmaster.com/catalog/129/3502/93070A120?s=5mm+screws)
 |  |  |  | TOTAL: | 179.42
PART NAME | Quantity | SPECIFICATION | Part NUMBER |  | SOURCING | UNIT PRICE | TOTAL PRICE | CONTRIBUTOR | LINK | NOTES
Corner Bracket | 6 | 1 3/8" length and width, 2 3/4" height, 0.06" thick, screw size no. 8 | 17715A73 |  | McMaster Carr | 3.07 | 18.42 | Carlos S. | https://www.mcmaster.com/brackets/corner-brackets-5/ | For mounting chassis corners
Corner Bracket | 6 | 1" width and length, 3/4" height, 0.04" thick, screw size no. 12 | 1564A1 |  | McMaster Carr | 1.22 | 7.32 | Carlos S | https://www.mcmaster.com/corner-brackets/corner-brackets-5/ | For mounting bottom plate
Corner Bracket | 5 | 1" length andd width, 1 1/4 height, 0.125" thick | 2313N36 |  | McMaster Carr | 7.24 | 58.35 | Carlos S | https://www.mcmaster.com/https%3A%2F%2Fwwwmcmastercom%2Fbrackets%2Fcorner-brackets-5/finish-your-own-corner-machine-brackets/ | Motor mounting
Cast acrylic sheet | 4 | 12" x 12" x 1/8", clear | 8774K11 |  | McMaster Carr | 49.28 | 197.12 | Carlos S. | https://www.mcmaster.com/cast-acrylic/clear-static-dissipative-scratch-and-uv-resistant-cast-acrylic/ | sides, bottom sheet
Timing Belt | 1 | XL Series Timing Belt, Trade No. 210xL025 | 6484K131 |  | McMaster Carr | 6.97 | 6.97 | Grayson V | LINK (https://www.mcmaster.com/drive-belts/xl-series-timing-belts-8/width~3-8-1/) | 3/8" Width // 0.200" Pitch
Corner Bracket | 1 | Corner Machine Bracket, Finish-Your-Own, 6061 Aluminum, 1" x 1" x 1-1/4" | 2313N36 |  | McMaster Carr | 7.24 | 7.24 | Carlos S. | LINK (https://www.mcmaster.com/corner-brackets/finish-your-own-corner-machine-brackets/)
Cast acrylic sheet | 2 | Cast Acrylic Sheet, 12" x 12" x 1/4", Yellow | 8505K74 |  | McMaster Carr | 10.78 | 21.56 | Grayson V (UNF) | LINK (https://www.mcmaster.com/catalog/129/4052/8505K754) | Include screw slots for horizontal adjustment // Design component to be flat
Ramp Element | 1 | Low-Carbon Steel Sheet, 12" x 12" x 0.0600" | 6544K53 |  | McMaster Carr | 20.47 | 20.47 | Grayson V (UNF) | LINK (https://www.mcmaster.com/catalog/129/4052/8505K754) | Circular near bottom, consider narrowing gap near top to filter objects toward center
TPU Spoke | 1 | Abrasion-Resistant Polyurethane Rubber Sheet, 12" x 12", 1/2" Thick, 40A Durometer | 8716K66 |  | McMaster Carr | 103.04 | 103.04 | Grayson V | LINK (https://www.mcmaster.com/catalog/129/4022/8716K66) | Design with screw hole (slotted into shaft) to save money on shaft collars
 |  |  |  |  |  | Total | 440.49
IEEE Mehcanical Part Order 2/22/23
NAME BRIEF | PART NAME | PART # | QTY | UNIT PRICE | TOTAL | SOURCE | Source Link
Shaft Pully | Corrosion-Resistant Timing Belt Pulley, XL, 3/8" Maximum Width, Hub, 2 Flange, 1.75" OD, 3/8" Shaft | 1277N28 | 1 | 16.65 | 16.65 | McMaster | LINK (https://www.mcmaster.com/catalog/129/1321/1277N28)
1/4" Washers | 316 Stainless Steel Washer for 1/4" Screw Size, 0.281" ID, 0.625" OD | 90107A029 | 1 | 8.51 | 8.51 | McMaster | LINK (https://www.mcmaster.com/products/washers/)
8020 Attachments | T-Slotted Framing, End-Feed Nut with Flanged Head, M5 Thread Size (4pk) | 5537T454 | 4 | 3.24 | 12.96 | McMaster | LINK (https://www.mcmaster.com/products/extrusions/t-slotted-framing-fasteners-4/rail-height~1/)
1/4" screws (.5" length) | Black-Oxide Alloy Steel Socket Head Screw, 5/16"-18 Thread Size, 1/2" Long | 90128A361 | 1 | 5.78 | 5.78 | McMaster | LINK (https://www.mcmaster.com/catalog/129/3491/91251A575)
Shaft Bushings | Light Duty Dry-Running Nylon Sleeve Bearing for 3/8" Shaft Diameter and 1/2" Housing ID, 3/8" Long | 6389K349 | 5 | 0.80 | 4.00 | McMaster | LINK (https://www.mcmaster.com/catalog/129/1403/6389K349)
Tensioner Bearings | Ball Bearing Shielded, Trade Number R4-2Z, for 1/4" Shaft Diameter | 60355K43 | 5 | 6.25 | 31.25 | McMaster | LINK (https://www.mcmaster.com/catalog/129/1384/60355K43)
Motor Mounts | Pololu 25D mm Metal Gearmotor Bracket Pair | N/A | 1 | 7.95 | 7.95 | Pololu | LINK (https://www.pololu.com/product/2676)
Acrylic sheets | Clear Scratch- and UV-Resistant Cast Acrylic Sheet, 12" x 12" x 1/8" | 8560K191 | 6 | 8.46 | 50.76 | McMaster | LINK (https://www.mcmaster.com/catalog/129/4052/8560K191)
1/16" Aluminum Sheet | Multipurpose 6061 Aluminum Sheet, 0.063" Thick, 12" x 12" | 89015K37 | 2 | 21.68 | 43.36 | McMaster | LINK (https://www.mcmaster.com/catalog/129/4159/89015K37)
Steel Ball Transfer | Steel Ball Transfer (21mm Height) | N/A | 3 | 2.99 | 8.97 | Servo City | LINK (https://www.servocity.com/5-8-roller-ball-transfer/)
PLA Roll 1.75mm | OVERTURE PLA Filament 1.75mm PLA 3D Printer Filament, 1kg Cardboard Spool (2.2lbs), (Purple) | N/A | 1 | 23.99 | 23.99 | Amazon | LINK (https://www.amazon.com/OVERTURE-Filament-Consumables-Dimensional-Accuracy/dp/B07VFQS5J3)
20mm 8020 | T-Slotted Framing, Single Four Slot Rail, Silver, 20 mm Square, Solid 3FT | 5537T101 | 5 | 13.10 | 65.50 | McMaster | LINK (https://www.mcmaster.com/products/8020/system-of-measurement~metric/t-slotted-framing-rails-4/single-rail-profile-style~four-slot/)
 |  |  |  | TOTAL: | 279.68
Part Name | QTY | Price | Adjusted Price
Closed Gusset Corner Bracket | 10 | 6.64 | 66.4
Corner Bracket 6060 Anodied Aluminum | 10 | 7.17 | 71.7
Tee Bracket Anodied 6105 aluminum | 8 | 17.77 | 142.16
*All parts sourced from Mcmaster Carr |  | Total: | 280.26
Purchase | Price
Cutting mats | 10.88
foam | 13.09
Zip-ties | 1.97
sandpaper | 7.88
gorilla glue | 7.48
electrical tape | 4.47
double sided tape | 18.94
small box | 1.48
nail files | 7
filament | 24

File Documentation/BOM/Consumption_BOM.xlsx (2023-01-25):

Name of Item | Description | Used in which subsystem(s) | Part Number | Manufacturer | Quantity | Price | Total | Link
Nvidia Jetson Nano | Top level controller | Top-level controller | 945-13450-0000-100 | Nvidia | 1 | 149.99 | 149.99 | https://www.amazon.com/gp/product/B084DSDDLT/
16 GB or larger UHS-1 microSD card | Storage device with the Jetson Nano (256 GB) | Top-level controller | LMSESXX256G-BNAEU | Lexar | 1 | 24.99 | 24.99 | https://www.amazon.com/Lexar-128GB-microSDXC-Memory-Adapter/dp/B08XQ97SK6
5V DC barrel jack power input cable | Standard barrel jack connector | Top-level controller | B07JGR7JJQ | SIOCEN | 1 | 9.99 | 9.99 | https://www.amazon.com/3-Pack-2-1mm-Power-Barrel-Connector/dp/B07JGR7JJQ
iClever DK03 Bluetooth Keyboard and Mouse | USB connection with a bluetooth chip | Top-level controller | B08KZXLTM6 | iClever | 1 | 39.99 | 39.99 | https://www.amazon.com/iClever-Bluetooth-Rechargeable-Ultra-Slim-Multi-Device/dp/B08KZXLTM6
Total |  |  |  | Total Components | 4 | Total Cost | 224.96

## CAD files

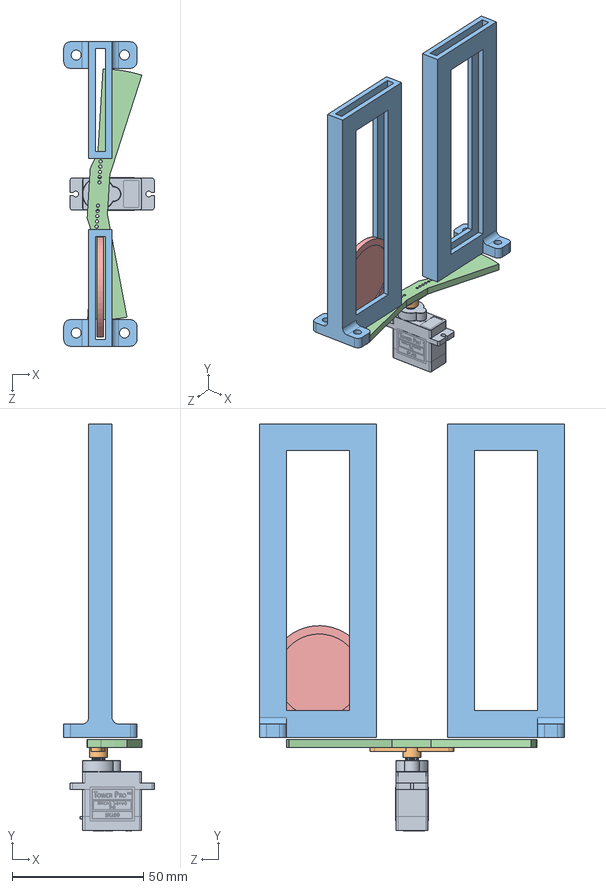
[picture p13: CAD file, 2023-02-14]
Documentation/3D Models/Feeding/Chip Dispenser Assembly.SLDASM
34.5 x 155.1 x 116.0 mm
SG90 - Micro Servo 9g - Tower Pro.1
SG90 - Micro Servo 9g - Tower Pro.3
Chip Silo x 2
Sweeper Arm
Chip

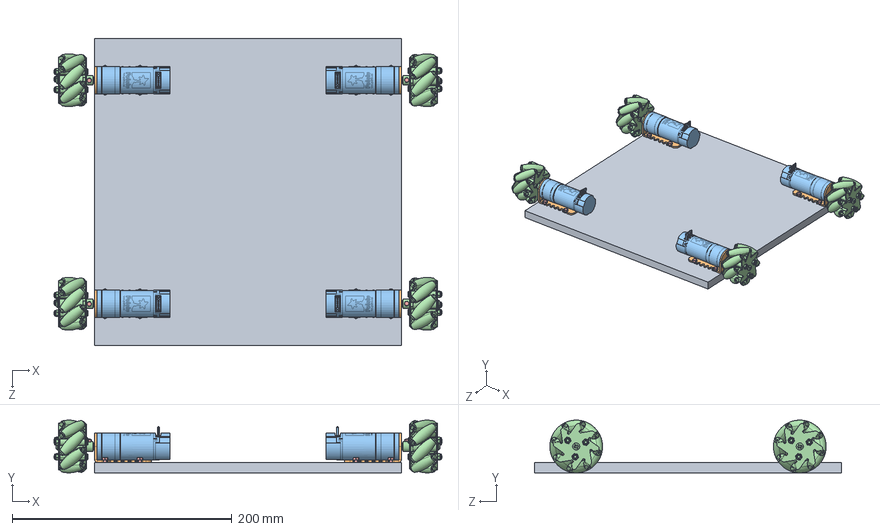
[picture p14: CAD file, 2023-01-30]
Documentation/3D Models/LocomotionSystem/Locomotion.SLDASM
353.4 x 48.0 x 279.4 mm
motor_Mount_plate
pololu-25d-mm-metal-gearmotor-bracket.step x 4
25d-metal-gearmotor-34-47-encoder.step x 4
48MM Steel Mecanum Wheel2 x 4
hex screw_am x 20

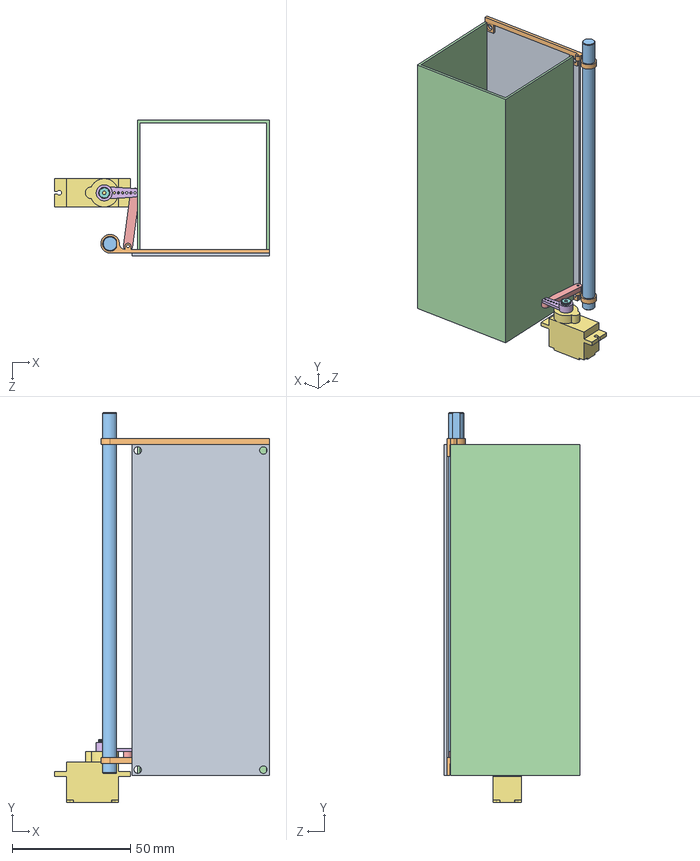
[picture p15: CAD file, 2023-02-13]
Documentation/3D Models/PedestalStorage/Cylinder_stacker_final.SLDASM
90.8 x 164.6 x 57.5 mm
window
door x 2
8632T132_D-Profile Rotary Shaft
silo
linkage
Servohorn
Pieza1
PZ2

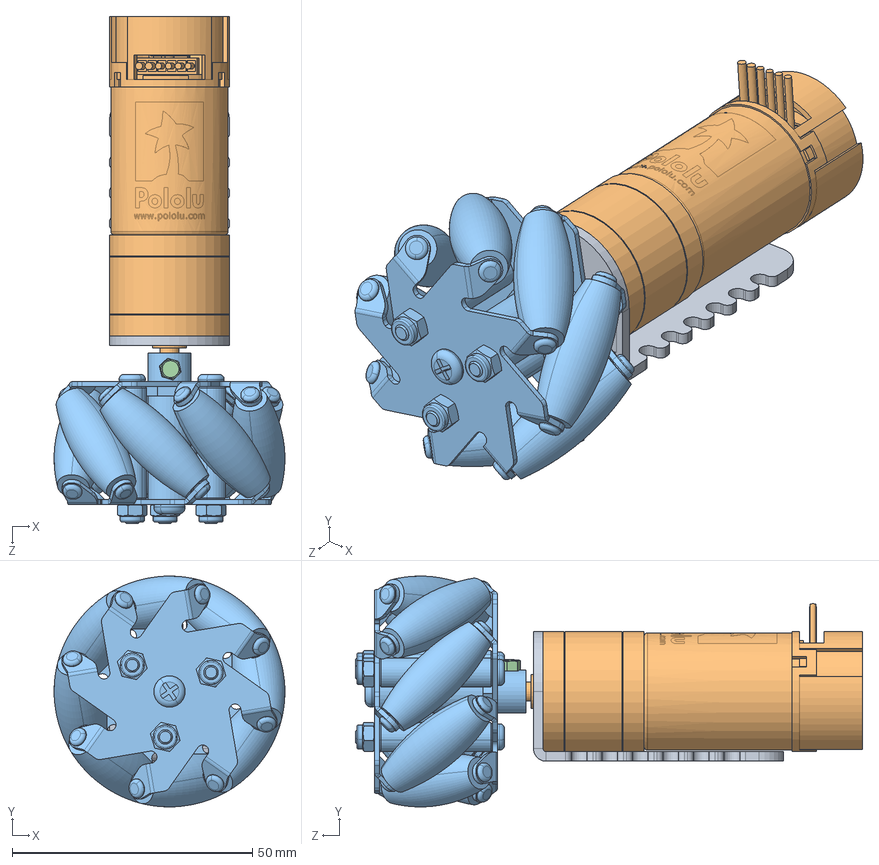
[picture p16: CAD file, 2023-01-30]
Documentation/3D Models/LocomotionSystem/Motor_Wheel_Assembly.SLDASM
48.0 x 48.0 x 105.4 mm
pololu-25d-mm-metal-gearmotor-bracket.step
25d-metal-gearmotor-34-47-encoder.step
48MM Steel Mecanum Wheel2
hex screw_am

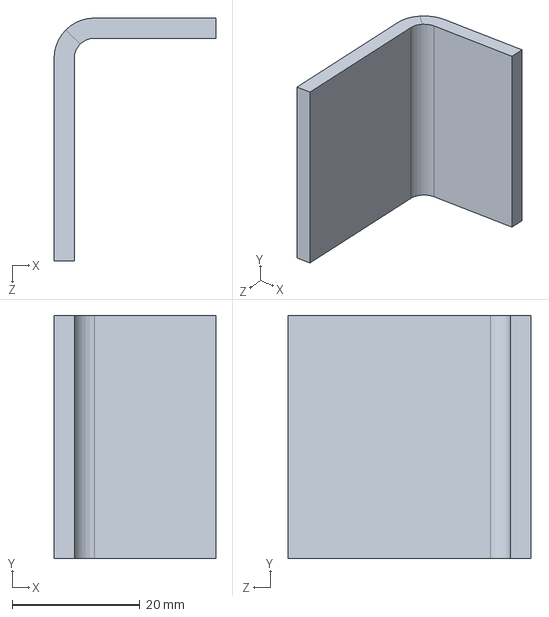
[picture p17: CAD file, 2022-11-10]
Documentation/3D Models/ConsumptionSystem/Intake_Assembly_11-9-222/Machine Bracket Motor Mount.SLDPRT
25.4 x 38.1 x 38.1 mm

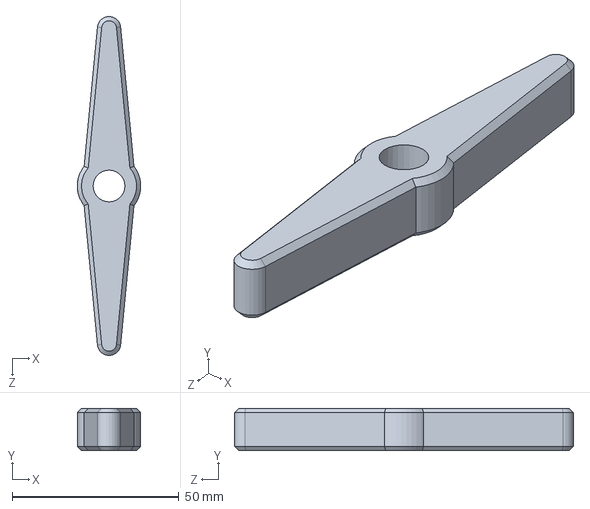
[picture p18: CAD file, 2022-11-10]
Documentation/3D Models/ConsumptionSystem/Intake_Assembly_11-9-222/TPU Spoke v0.1.SLDPRT
19.0 x 12.7 x 101.6 mm

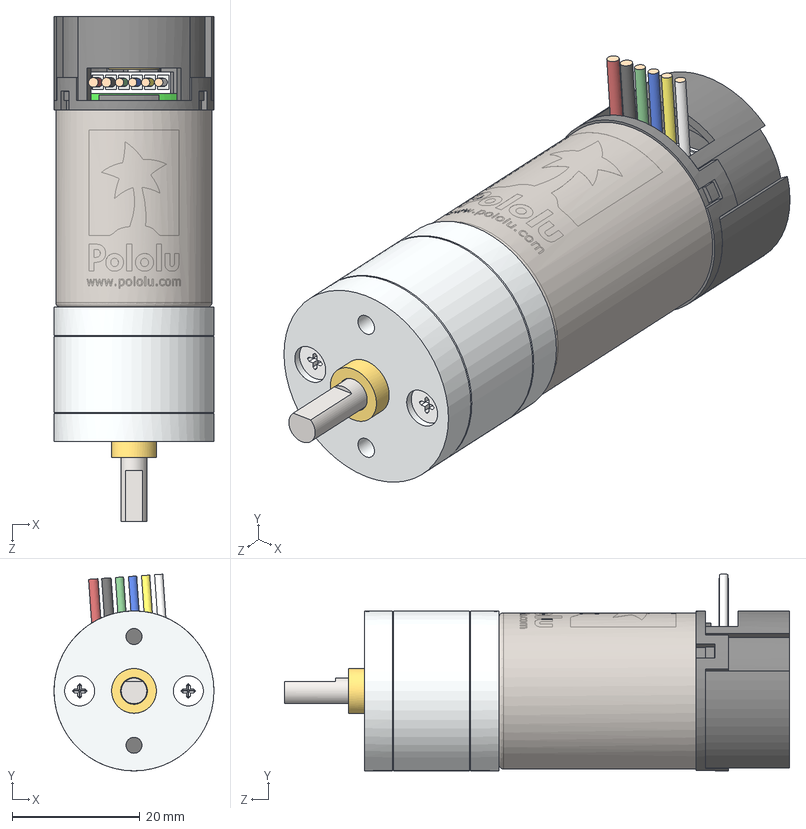
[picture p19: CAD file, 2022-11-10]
Documentation/3D Models/ConsumptionSystem/Intake_Assembly_11-9-222/25d-metal-gearmotor-34-47-encoder.step
25.0 x 30.8 x 79.0 mm

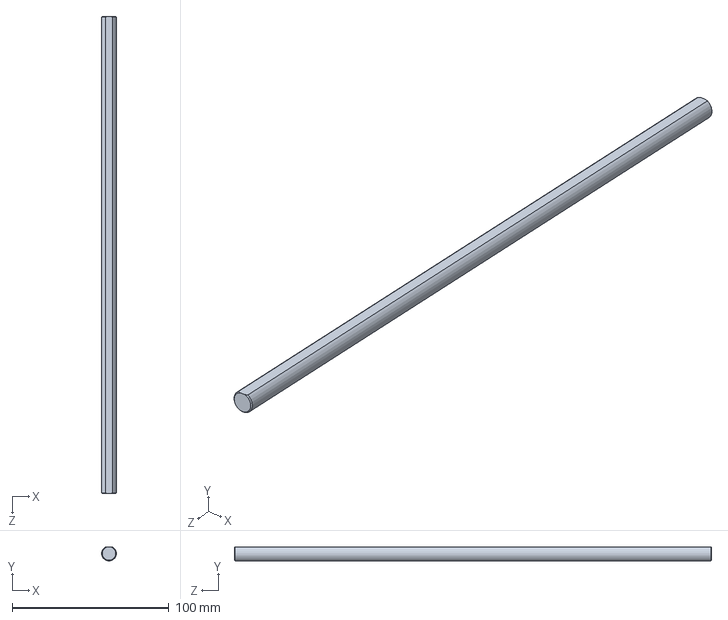
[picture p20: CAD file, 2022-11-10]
Documentation/3D Models/ConsumptionSystem/Intake_Assembly_11-9-222/8632T1_D-Profile Rotary Shaft.SLDPRT
9.50 x 8.85 x 304.8 mm

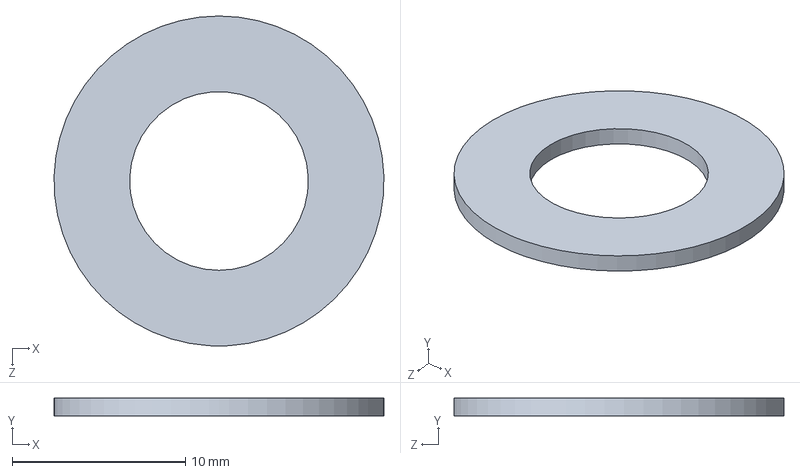
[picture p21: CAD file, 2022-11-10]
Documentation/3D Models/ConsumptionSystem/Intake_Assembly_11-9-222/90107A127_316 Stainless Steel Washer.SLDPRT
19.0 x 1.02 x 19.1 mm

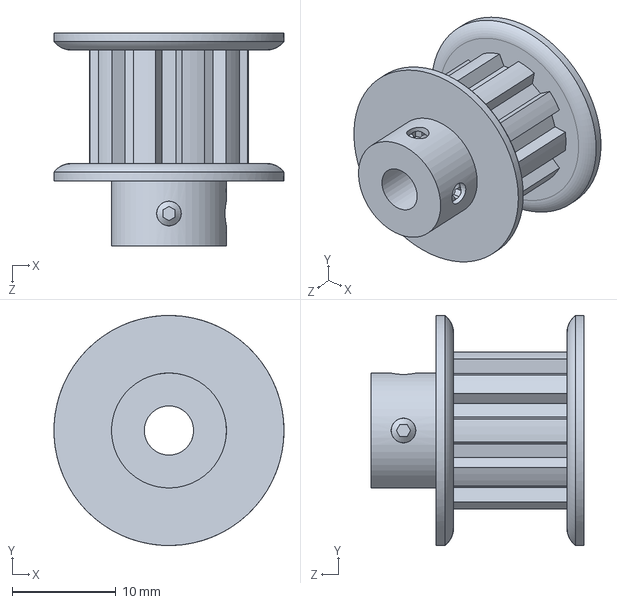
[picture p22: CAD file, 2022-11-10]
Documentation/3D Models/ConsumptionSystem/Intake_Assembly_11-9-222/1277N41_Corrosion-Resistant Timing Belt Pulley.SLDPRT
22.2 x 22.2 x 20.6 mm

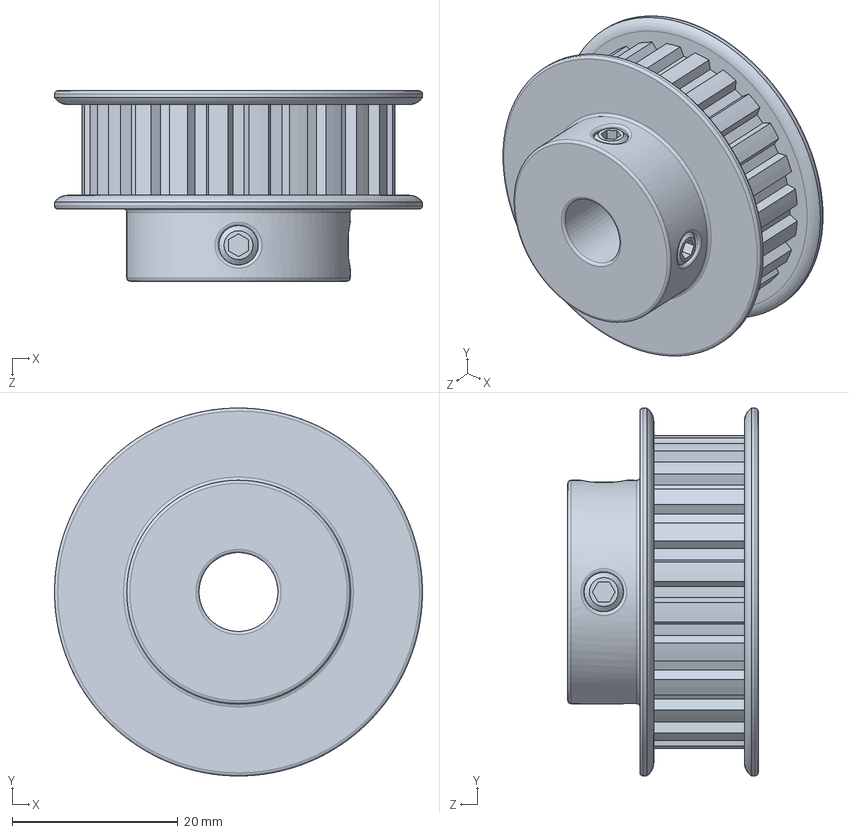
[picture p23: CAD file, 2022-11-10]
Documentation/3D Models/ConsumptionSystem/Intake_Assembly_11-9-222/1277N28_Corrosion-Resistant Timing Belt Pulley.SLDPRT
44.5 x 44.4 x 23.0 mm

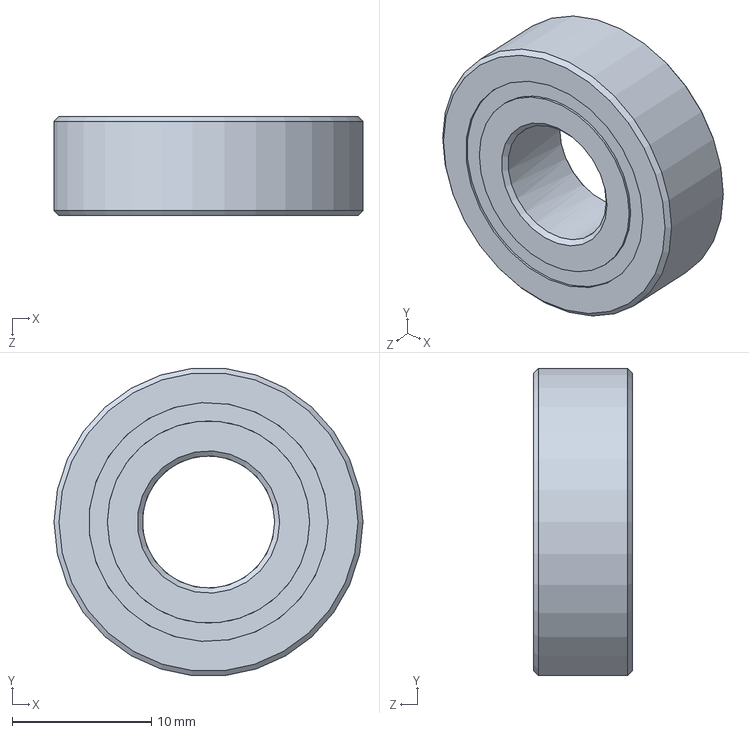
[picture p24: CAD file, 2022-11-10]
Documentation/3D Models/ConsumptionSystem/Intake_Assembly_11-9-222/60355K45_Ball Bearing.SLDPRT
22.2 x 22.1 x 7.14 mm

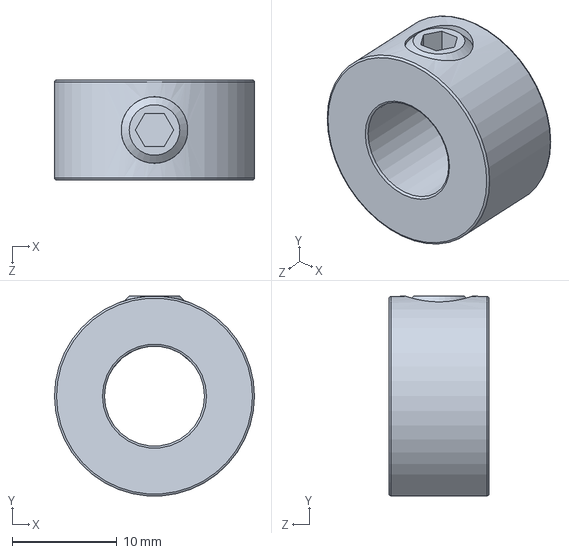
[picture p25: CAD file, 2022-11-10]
Documentation/3D Models/ConsumptionSystem/Intake_Assembly_11-9-222/9414T8_Set Screw Shaft Collar.SLDPRT
19.1 x 19.0 x 9.53 mm

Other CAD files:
Documentation/3D Models/ConsumptionSystem/Intake_Assembly_11-9-222/Intake Side Pannel v0.1.SLDPRT
Documentation/3D Models/ConsumptionSystem/Intake_Assembly_11-9-222/Intake Timing Belt.SLDPRT
Documentation/3D Models/ConsumptionSystem/Intake_Assembly_11-9-222/Intake Ramp Element.SLDPRT
Documentation/3D Models/ConsumptionSystem/Intake_Assembly_11-9-222/25d-metal-gearmotor-34-47-encoder.step.SLDPRT
Documentation/3D Models/Chassis/Chassis_Fit/Aduino.ipt
Documentation/3D Models/Chassis/Chassis_Fit/Arduino2.ipt
Documentation/3D Models/Chassis/Chassis_Fit/Assembly2.iam
Documentation/3D Models/Chassis/Chassis_Fit/Chips.ipt
Documentation/3D Models/Chassis/Chassis_Fit/Intake.ipt
Documentation/3D Models/Chassis/Chassis_Fit/Jetson.ipt
Documentation/3D Models/Chassis/Chassis_Fit/Pedestal.ipt
Documentation/3D Models/Chassis/Chassis_Fit/Sorting.ipt
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

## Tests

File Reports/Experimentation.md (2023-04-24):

# **Experimental Analysis**

### **Cut Subsystems and Justification**

The following subsystems have been cut since the beginning of the project:
- Sorting
    - Due to size constraints and the parts for this subsystem not arriving, this subsystem was cut.
- Duck Storage and Delivery
    - The project was rescoped before the competition and the duck storage and delivery subsystem did not make it into the final implementation. This decision was made unanimously by the team at the competition. It was determined that the duck storage and delivery system, while well designed and theoretically functional, could not be reliably implemented before the competition. 
- Pedestal Storage and Delivery
    - Due to size constraints and the parts for this subsystem not arriving, this subsystem was cut.
- Vison
    - Due to the parts for this subsystem not arriving, this subsystem was cut.
- Consumption (repurposed - now called Delivery Subsystem)
    - The project was rescoped before the competition and the consumption subsystem did not make it into the final implementation. This decision was made unanimously by the team at the competition. The team decided to transition the consumption subsystem into the delivery subsystem. The direction of the motor was changed to push instead of consume, and the subsystem was used to push what items had been collected into the recycling area.

The following shall statements were closely related to these subsystems and therefore will not be discussed in this experimental analysis document:

- Shall design a robot which can find and move 90% of
the ducks into a holding area connected to the robot.
- Shall locate the duck pond in the center of the arena
within plus or minus one inch of error tolerance.
- Shall transport and place 90% of the ducks stored inside
the holding area to their final location in the duck pond.
- Shall find and move at least five pedestals into an internal
holding area inside the robot.
- Shall assemble one statue that is three pedestals tall and
one statue that is two pedestals tall using all five pedestals
obtained in order to maximize points obtained based on
discussion in weekly meetings.
- Shall place statues entirely inside the white inner circles
within plus or minus one inch of error tolerance.
- Shall place remaining unused pedestals that are held after
the five required pedestals have been obtained within the
internal holding area inside the robot.
- Shall move the extra pedestals obtained over the five
required pedestals in the recycling area.

## **Constraints from Signoffs:**

### **Full run from competition [here](https://www.youtube.com/watch?v=IqyCZeEZ9IM&t=77s)**

## **General results from runs at the competition:**

For each run, there were ten ducks and seven pedestals randomly distributed on the arena as well as six food chips (3 red and 3 green) that the team could pre-load before the run started. The team had three minutes after the start switch was flipped to get as many points as possible. The results from these runs are shown below.



| Round | Green chip | Red chip | Cylinder Recycle | Duck Recycle | Duck Pond | Grand Total Points |
| ----- | --- | --- | --- | --- | --- | --- |
| 1 | 3 | 3 | 1 | 4 | 0 | 52 |
| 2 | 3 | 3 | 0 | 0 | 0 | 42 |
| 3 | 2 | 3 | 0 | 0 | 0 | 35 |
| 4 | 2 | 2 | 4 | 6 | 0 | 48 |
| 5 | 3 | 3 | 4 | 1 | 0 | 52 |
| 6 | 2 | 2 | 1 | 2 | 1 | 39 |

Below is the number of points scored in each round of the competition. If we had integrated the all functionality targeted after the rescope, we would have scored 86 points each round. 

Recycling: $2\ points * 17\ objects = 34\ points$

Feeding: $6\ correct chips * 7\ points = 42 \ points$

Fireworks: $1\ fireworks\ switch\ flip * 10\ points = 10\ points$

Total: $86\ points$



## **Feeding results:**

- **Purpose of Experiment**

For this experiment, the team intends to measure the accuracy of the chip feeding mechanism implemented on the robot. 

- **Description**

Experimentation was conducted during the runs at the competition. 

For each run, there were ten ducks and seven pedestals randomly distributed on the arena as well as six food chips (3 red and 3 green) that the team could pre-load before the run started. The team had three minutes after the start switch was flipped to get as many points as possible. The robot had to navigate the field autonomously and no one could intervene on the robot in anyway or the round would end. 

- **Expectation (Prediction)**

The expectation for this experiment was to consistently delivery food chips reliably. The team tested the robot in the build up to the competition and the robot was able to reliably deliver the food chips with error only on every third run. 

- **Number of trials** 

The number of trials for this experiment was the number of round played at the competition, which was 6. 

- **Results** 

The design has been changed to two separate cups with two separate servo motors in order to simplify the design. The cups are only big enough to hold the chips, and are mounted on the servo motors which are mounted on the outer edge of the robot, thus saving much needed space inside the robot.

The food chip dispensers can be seen in the image below. They are located on the top crossbar of the robots chassis. They consist of a cup connected to a servo motor.



Below is the final experimentation taken during the competition, we consistently delivered food chips, but did not meet the idealized goal of delivering 100% of the food chips correctly all of the time. 



- Since the design has been simplified in order to save time, the servos do not need to have as much torque. However, they have much more than sufficient torque needed to flip the cups and dump the chips during the competition. Servos purchased met requirements based on analysis performed in sign offs.

- **Interpretation**

Feeding was able to meet a high standard, but was unable to meet the 100% standard written in our project proposal. It can be seen from the results above that many of the points scored in the competition were from the feeding mechanism. 

In hindsight, the expectation for feeding from the project proposal was too high a standard, because it was very unlikely that this could have delivered the chips correctly in every attempt. 

## **Locomotion results:**

### **Experiment #1: Weight**

- **Purpose of Experiment**

The purpose of this experiment was to measure the weight of the robot. This was too confirm that the weight constraint from the locomotion sign off was met in the final implementation. 

- **Description**

The weight was a constraint of the locomotion subsystem due to the weight limitation of the mecanum wheels that we purchased. This weight constraint was that the robot needed to be < 10.376 kg.

- **Expectation (Prediction)**

Due to the analysis doe in the sign off for locomotion, the team was confident that the robot met the weight constraint that is being tested in this experiment. The expectation for this experiment was that the robot would fall within the weight constraint defined. 

- **Number of trials** 

The team weighed the robot six times on the scale in the machine shop in the basement of Brown and the robot weighed 14 pounds. 

- **Results** 

- **Weight of the robot**

The final competition robot weight was $14\ pounds\ or\ 6.35029\ kg\ \lt\ \approx\ 10.376\ kg$. 

This means the final weight of the robot was within specification defined in the constraints for the project. 

- **Interpretation**

It can be seen that the robot fell well within the weight constraints defined in the sign off for locomotion. This constraint has been verified to have been met in the final implementation. 

### **Experiment #2: Velocity**

- **Purpose of Experiment**

The purpose of this experiment was to verify that the velocity achieved in the arena is greater than the minimum required speed defined in the locomotion sign off.

- **Description**

Locomotion subsystem speed was set using a PID controller running on the Arduino Mega2560. The speed was represented in rotations per minute (RPM). 

- **Expectation (Prediction)**

The expectation from this experiment is that the robot moved faster than the minimum speed defined in the locomotion sign off. 

- **Number of trials** 

The number of trials for this experiment was 6 for each round completed in the competition. 

- **Results** 

***Max Speed***

$\frac{150\ rotations}{1\ min} * \frac{1\ min}{60\ sec} * \frac{48\pi\ mm}{1\ rotation} * \frac{0.00328084\ feet}{mm} = 1.24 \frac{feet}{sec} \gt 0.0677 \frac{meter}{sec} = 0.222 \frac{feet}{second}\ (minimum\ speed\ requirement)$

***Typical Competition Speed***

$\frac{100\ rotations}{1\ min} * \frac{1\ min}{60\ sec} * \frac{48\pi\ mm}{1\ rotation} * \frac{0.00328084\ feet}{mm} = 0.825 \frac{feet}{sec}$

- **Interpretation**

Experimentation above shows that the speed of the robot in the arena satisfied the minimum speed requirement defined in the locomotion sign off. 

## **Power results:**

### **Experiment #1: Battery Voltages**

- **Purpose of Experiment**

The purpose of this experiment was to verify that the power subsystem will supply the proper voltage to the subsystems that require a certain voltage level.

- **Description**

The multimeter was used to verify the output voltage of the DC/DC regulator while connected to the entire system to make sure the regulator output a steady 12 V output.

- **Expectation (Prediction)**

The team expects that the voltage output of the DC/DC regulator while connected to the entire system to be a steady 12 V output.

- **Number of trials** 

The number of trials for this experiment was 6 for consistency throughout the analysis.

- **Results** 
 
The output of the TalentCell battery is regulated by the DC-DC Converter and provides a nearly constant 12 V to sufficiently power all components connected to it including the buck converter to the servo motors and the buck converter connected to the Jetson.

The multimeter measured around 11.95 V each trial. 



The main power bus in the robot was supplied from two 6 V MightyMax batteries in series. This bus was connected to all the locomotion DC motor drivers. One of these 6 V battery was used to power the 6 V motor driver for the delivery subsystem. A separate bus was created for powering the Jetson and the servo motors, and it was supplied from the 12 V TalentCell battery. All power connections had a common ground. 

The multimeter was connected to the output of the buck converter while connected to the rest of the system to verify.



Further measurements were made on the 6 V batteries to verify the voltages of the batteries with just one of the batteries and both in series. The batteries were connected to the system as a whole and they were under load.





- **Interpretation**

The battery is sufficient in providing 12 V and over 2 A to meet the robot’s needs. This was achieved with the original 12 V TalentCell battery as well as two 6 V MightMax batteries connected in series.

### **Experiment #2: Buck Converter Noise**

- **Purpose of Experiment**

One of the constraints for this subsystem was that noise from the buck converters would be eliminated. LC filters were added to reduce this noise.

- **Description**

Measurements were taken using an osciloscope that was connected across the output of the buck converter both before and after the filter.

- **Expectation (Prediction)**

It was expected that the noise would be eliminated after the filter was applied.

- **Number of trials** 

Five different trials were run.

- **Results** 

Below is images of the noise before and after the filter was applied. The image for after the filter is the best result.

Before filtering:



After Filtering:





- **Interpretation**

The noise after adding the filter is less significant than without the filter. Though the filter did not eliminate noise, but the peak to peak voltage is significantly lower and the noise signal overall is cleaner. The peak to peak voltage of the noise before the filter was around 400 mV whereas after the filter it was 150 mV or lower per trial.

## **Delivery Subsystem (was called Consumption) results:**

- **Purpose of Experiment**

The purpose of this experiment is to test the results of the delivery subsystem to getting items to the recycling area during the competition. Each item in the arena, food chips, ducks, and pedestals were all worth the same amount of points. 

- **Description**

This experimentation was taken during the competition rounds in Orlando.

For each run, there were ten ducks and seven pedestals randomly distributed on the arena as well as six food chips (3 red and 3 green) that the team could pre-load before the run started. The team had three minutes after the start switch was flipped to get as many points as possible. The robot had to navigate the field autonomously and no one could intervene on the robot in anyway or the round would end. 

- **Expectation (Prediction)**

The expectation for this experiment was that the robot would effectively push multiple items into the recycling area. The decision to shift to the pusher happened at the competition. We expected to average items in recycling after the round to be 3.5 items.

- **Number of trials** 

The number of trials for this experiment was the number of round played at the competition, which was 6.

- **Results** 

Many variations of spokes have been tested in order to see which ones work the best. The only spokes that were used in the final implementation were curved TPU spokes, and those can be seen in the final total robot CAD model in this document. 

The size of the final delivery implementation was 5.25"x9.25"x11.75" (LxWxH). The delivery mechanism is large enough for a duck to be consumed as well as the pedestals, while also being within specification for the robot size set by the competition.

Note: In the final implementation in the competition, no ducks or pedestals were consumed. The motor direction of the delivery motor was reversed and the consumption was converted into a pusher. The robot collected objects in the arena on the consumption ramp, and then the spokes pushed out the objects into the recycling. 

There are three walls surrounding the intake in order to protect any limbs from moving parts. This was a safety feature implementation based on considerations made during detailed design. 

The chart below conveys the effectiveness of the delivery subsystem on the robot. 



- **Interpretation**

The resulting average items in recycling after each round during the competition was $\frac{5+0+10+5+4}{6}$. This is very close the predicted outcome in the prediction above. It can be seen however that the implementation was quite volatile in practice. 

Rounds 2 & 3 were bad throws in the randomness of the items around the arena. The robot performed better if the items were thrown towards the switch because of our path implementation. We turned a lot around the feeding area getting the chips to the red and green feeding areas and our path sweeped towards the switch from the feeding areas so if they were on that side of the board they were significantly more likely to get pushed closer to the recycling area. 

## **Fireworks results:**

- **Purpose of Experiment**

The purpose of this experiment was to demonstrate that the robot was able to flip the switch. 

- **Description**

This experiment as conducted in the Capstone Lab on the board that we built for testing. 

- **Expectation (Prediction)**

The expectation for this experiment was that the robot would have the force to flip the switch as analyzed for in the sign offs for fireworks, but that it would not reliably flip the switch consistently due to in precision in the path and position of the robot. 

- **Number of trials** 

The number of trials for this experiment was the number of round played at the competition, which was 6.

- **Results** 

The robot did not flip the switch during the competition, but did have the force needed to flip the switch.

The robot has the force necessary to flip the switch without issue, though it did not flip the switch during the competition. 

Video Demonstration of the Fireworks Switch [here](https://www.youtube.com/watch?v=TUixtoiBSds)

- **Interpretation**

The robot was unable to flip the switch in the competition, but did have the force necessary to do so. 

The issue of not being able to flip the switch was a path script that was not perfected to flip the switch in the arena at the competition. We also did not have LIDAR sensors that we ordered that could have been used for the robot to locate itself in the arena precisely.  

## **Measures of Success from Project Proposal**
- The team rescoped and decided not to start using the LED indicator to instead focus on other subsystems. A start switch was added to replace this functionality. 

- The robot was unable to drop all the chips in the correct location on every competition run. A table showing all points scored is shown in the feeding section under the shall statements.

- The project was rescoped to remove duck storage and therefore did not collect and store any ducks. They were instead be pushed to the recycle area.

- The robot was unable to flip the light switch during the six competition rounds. The python script has been written as well as the video has been made as of March 10, 2023.

- Due to the sorting, consumption, and pedestal storage subsystems being cut or repurposed, the pedestals will no longer be consumed, sorted, or stacked. Instead, pedestals will be pushed to recycling just like the ducks.

- The robot's path was altered to push as many objects as possible into the recycle area, instead of placing any remaining items into the recycle area.

## **Shall Statements**

### **Power:** 

- Shall design an autonomous robot with a single start
button, allowing the robot to start moving through its
environment.

    - The start button was implemented as a start switch. This starts the path for the robot. This is shown in the full round video at the top of this document. 
    
- The robot will have a single emergency stop button at a
point that is easily accessible and can be safely reached,
which will shut down all physical movement performed
by the robot in the case of an emergency.

    - The E-stop button is easily accessible on the top of the robot. The switch cuts all power to the dc motors for locomotion and delivery. his is shown in the full round video at the top of this document.

- Shall create an easily reachable (not blocked by motors,
chassis, wheels, or any other object) emergency cut off
switch to allow the team to disable the robot in the case
of an emergency.

    - The E-stop button is easily accessible on the top of the robot. his is shown in the full round video at the top of this document.

- Shall have a self-latching emergency stop push-button
that has a positive operation. The button shall not be a
graphical representation or a flat switch based on NFPA
79 - 10.7.2. [1] This constraint addresses the need for the
addition of practical engineering standards.

    - The E-stop button chosen meets these specifications.
    


Video demonstration of E-stop [here](https://www.youtube.com/watch?v=tuQbhPMOLbw).

- Shall abide by the Department of Energy Standard 79
FR 7845 in the team’s purchase or design of wall warts
for energy conservation and efficiency. [3] This constraint
addresses an ethical consideration by better ensuring the
safety of the team and all others interacting with the robot
as well as the addition of ethical standards.

    - The wall wart bought with the TalentCell battery abides by this standard.

### **Software:**

- Shall represent knowledge using IEEE standard IEEE
1872-2015 Ontologies for Robotics and Automation used
to represent knowledge about the typography of the arena.
This ontology will be used to represent relationships
between the landmarks in the area and what is known.
It should not change during the competition, so it can be
predefined. [2]

    - We ended up using encoder distances to represent the movement and position in the arena. This was written during the conceptual design when we had been considering using SLAM to navigate the arena area. 

### **Feeding:**

- Shall design an autonomous robot that will earn all
possible points for delivering 100% of the correct food
chips to both the manatees and alligators.

    - This was accomplished in the first two rounds of the competition, but was not accomplished in the later rounds of the competition. 

### **Fireworks:** 
- Shall design an autonomous robot that will be able to flip
a switch from left to right.

- Shall design an animated fireworks MPEG video and
write a Python script that will play the video when
activated by the switch.

    - This fireworks video was created, and won second place in a separate competition for most creative fireworks video. It was judged based on creativity and school spirit. 
    
### **Chassis:**
- Chassis will be designed with an aluminum frame. Alu-
minum is abundantly available under the earth’s surface
and mining can be offset with post-mining rehabilitation
and efficient recycling. This constraint will lessen the
broader impact the team has on the environment.

    - The chassis was constructed using Aluminum extrusion 80 x 20.

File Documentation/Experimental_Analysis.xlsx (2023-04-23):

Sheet: Sheet1
Round | Green chip | Red chip | Cylinder Recycle | Duck Recycle | Duck Pond
1 | 3 | 3 | 1 | 4 | 0
2 | 3 | 3 | 0 | 0 | 0
3 | 2 | 3 | 0 | 0 | 0
4 | 2 | 2 | 4 | 6 | 0
5 | 3 | 3 | 4 | 1 | 0
6 | 2 | 2 | 1 | 2 | 1
Round | Grand Total
1 | 52 | 86
2 | 42 | 86
3 | 35 | 86
4 | 48 | 86
5 | 52 | 86
6 | 39 | 86

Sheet: Sheet3
Power Measurements
Trial
1 | 11.94
2 | 11.94
3 | 11.95
4 | 11.95
5 | 11.95
6 | 11.95
Trial
1 | 5.213
2 | 5.213
3 | 5.212
4 | 5.212
5 | 5.212
6 | 5.212
Trial
1 | 6.62
2 | 6.61
3 | 6.518
4 | 6.519
5 | 6.518
6 | 6.517
Trial
1 | 13.09
2 | 13.09
3 | 13
4 | 13
5 | 12.99
6 | 12.98
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

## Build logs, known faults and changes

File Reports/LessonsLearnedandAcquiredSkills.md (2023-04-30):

# Lessons Learned

# Madison Kelly

Reflect on the project, both technical and organizational. What went well? What didn’t go well? 

- I believe our teamwork was very good and we worked well together. 
- I think making quick decisions to cut subsystems that were not working properly could have improved.

What unanticipated problems occurred? 

- There were many issues that occurred during the competition in Orlando including fried arduinos and completely redesigning the power subsystem. I was proud that the team was able to overcome these problems given the time constraint.
- There were also many issues with ordering. 

What would you do differently if you were to do it over again? 

- I would not chose a battery with a current limit.
- I would make sure we got a chassis to do practice runs as early as possible.

What “best practices” have you identified? 

- Check the schematic designs that were made in the initial planning of the project when building the actual robot. 
- Make sure you document everything.
- Label voltages of the wires.

What words of wisdom would you pass on to future students?

- Use your resources! 
- Go for the more ambitious plan at first, and then scale back. You never know what might work and what might not.

What new knowledge or skills did you acquire throughout capstone.

- Importance of knowing the theory of the electrical components you plan to use. 
- Technical knowledge of different components.
- How to overcome problems that seem insurmountable.
- Basics of power subsysems for robotics.

# Mark Beech

Reflect on the project, both technical and organizational. What went well? What didn’t 
go well? 

- Our teamwork and communication was very good across the team. We worked together well and got the job done. Our team's designs were well thought out and were rarely half baked during the detail design phase especially. 
- Our ability to work in parallel in the prototype and experimentation phase was not the best. We could work as a group just fine, but when it came to splitting up the work we struggled to divide the work well. Later in the project lifecycle, we had the tendency to rush things and not think things through as much as we did in the detail design phase. This was mainly due to the time crunch of the competition deadline.

What unanticipated problems occurred? 

- The ordering issues were not anticipated at all. I thought some stuff may have shown up late, but I never expected to not get entire subsystems worth of parts. There were also many problems the team ran into at the competition in Orlando such as bricked arduinos, torque issues, path issues, and last minute redesigns.
- There were many issues with solder joints and other connections as well as routing wires within the small chassis of the robot that quickly became a headache.

What would you do differently if you were to do it over again? 

- The team worked very well together, but I wish we were able to work in parallel much better. Typically, we would all work on the same one or two tasks. This slowed our progress quite a bit in hindsight.
- I would not buy a battery with a current limit to control motors in robotics. Going ahead and designing seperate power sources for the controllers and the motors would have saved a lot of headache.
- The wires in the robot were a complete mess due to the rush and it ended up causing many problems when it came to debugging anything wrong with the robot. This issue also caused the robot to not function properly sometimes due to solder joints being bad or wires falling out that we could not see or get to easily.

What “best practices” have you identified? 

- Planning and communication within the team are keys to success. 
- Always double check everything including schematic designs, code, and solder jobs.
- Never assume something will work the first time
- Good decumentation and color coding is a lifesaver for debugging

What words of wisdom would you pass on to future students?

- Be sure to think things through with how one part of a design could effect other parts of the design that most would not think is connected in any way.
- If something doesn't work, it doesn't mean it was pointless. Usually, you learn something valuable even from the failures that come with designing anything.
- It is better to think something through than rush to try to implement it.

What new knowledge or skills did you acquire throughout capstone.

- The importance of the planning phase.
- Basics of ROS and Linux
- How to present a technical topic well
- How buck/boost converters work

# Nathan Gardner

Reflect on the project, both technical and organizational. What went well? What didn’t go well? 

- I think the project was well organized. We had technical issues arise when we faced ordering issues. We faced many technical issues based on deadlines for the competition and had to work to the very end to have a competitive bot at the competition.

What unanticipated problems occurred? 

- We had many unanticipated issues between the conceptual/ detailed design phase and the build phase. The team had ideas of how things would work but in practice they did not work as we intended. 
- We had to adapt to issues as they arose and had to rescope the project due to unforeseen technical issues. 

The team planned for possible issues being aware of the breadth of scope in the problem statement. 

- The team overcame many technical issues in the 48 hours leading up the competition including: power redesign, burnt out components, and consumption redesign. 

What would you do differently if you were to do it over again? 

- I would have liked to have all parts ordered earlier given the ordering issues that arose in the second semester. 
- Given the knowledge that I have now looking back on the project and seeing opponents robot strategies, I would have rescoped earlier and built the entire chassis around the idea of being a pusher robot. The winning team at the competition fed the food chips successfully and then had arms that extended and swept the whole arena in one pass and moved all objects to the recycling area. 

What “best practices” have you identified? 

- Good communication and planning
- Ensure everyone has a subsystem they are able to contribute too using their pas experiences
- Communication throughout the project is required for systems to integrate at the end of design

What words of wisdom would you pass on to future students?

- Obviously try your hardest to follow best engineering practices when building up the project, but be sure to develop plans for when things break or do not work as intended. 
- Do not give up whenever things break and do not work as intended, develop a strategy with what you have and move forward. 

What new knowledge or skills did you acquire throughout capstone.

- Team/ project leadership
- Robot operating system (ROS) experience
- Systems engineering lifecycle and design understanding
- Project work across disciplines (electrical, computer, and mechanical engineering)

# Luke McGill
Reflect on the project, both technical and organizational. What went well? What didn’t go well? 

- The team had good communication during the design of the project. We all collaborated and helped each other out wherever.
- The ECE team and the ME team had some difficulties lining up our designs. We could have communicated better and planned our work accordingly.

What unanticipated problems occurred? 

- We had some issues ordering parts. Some ordered parts never arrived, causing us to have to change our design in some areas.

What would you do differently if you were to do it over again? 

- I would have chosen a more powerful power supply. We underestimated the load that the robot would take. A larger power supply would have solved several issues that we had to work around.
- Several of our parts were not very good quality. The power busses we chose were not best suited for small wires like the ones we were using. I also would have chosen different perf boards. The ones we chose had rails instead of individually adressable holes for soldering.

What “best practices” have you identified? 

- Debugging as you go is so important. If you wait to test your project until after you have completed a large chunk, it is much more difficult to identify issues.
- Tape every single exposed wire. This will prevent any accidental shorts.
- Use flyback diodes on all components that draw any significant power.

What words of wisdom would you pass on to future students?

- Try your best. You will be suprised of what you are capable of when you put your all into something. Even when you hit a wall, keep attacking the problem and eventually you will find a solution.
- Be willing to put in the work for your capstone project. Don't settle for having a mediocre project when it could have been a great project given the work be put in.

What new knowledge or skills did you acquire throughout capstone.
- I furthur developed my software skills. I learned a little about ROS. I also helped implement a PID controller in c++ which was a new concept to me.
- I learned how good teamwork can help, as well how poor planning and communication can hurt the project.

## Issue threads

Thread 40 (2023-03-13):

feature_pid_locomotion ROS communication

nathan-gardner, 2023-03-13:
This issue is associated with PR #39

**Describe the problem**
The PID locomotion control branch is seemingly non-deterministically not responding to publishing in the ROS computation graph. It is very noticeable in the /locomotion/cmd_vel topic because the robot is sometimes not responding to commands for changing the velocity.

**Where to go to find the problem**
[here](https://github.com/nathan-gardner/CapstoneRepo/tree/feature_pid_locomotion/Software/mega2560/mega1)

**Screenshots**
N/A

**Additional context**
main branch does not seem to have this as a major issue when testing. I would start with a diff between pid_feature_locomotion and main.

nathan-gardner, 2023-04-21:
This error was a publication error on the python client side and was resolved before the competition.

Closed 2023-04-21.

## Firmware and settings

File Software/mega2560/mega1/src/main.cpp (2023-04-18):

/**
 * @file main.cpp
 * @author Nathan Gardner
 * @brief Main driver file
 * @version 0.2
 * @date 2023-01-21
 *
 * @copyright Copyright (c) 2023
 *
 */

#ifndef MAIN_CPP
#define MAIN_CPP

#include <Arduino.h>
#include <ros.h>

#include <locomotion.h>
#include <feeding.h>
#include <consumption.h>
#include <duckstorage.h>
#include <start.h>

ros::NodeHandle nh;



/**
 * @brief Setup code for Arduino boot
 *
 */
void setup()
{
  nh.initNode();

  locomotion::init(&nh);
  feeding::init(&nh);
  consumption::init(&nh);
  DuckStorage::init(&nh);
  start::init(&nh);

  Serial.begin(115200);
}

/**
 * @brief Loop that is run continually while the Arduino is powered on
 *
 */
void loop()
{
  start::read();
  locomotion::updateEncoder();
  locomotion::updateVelocity();
  start::updateStart();
  locomotion::computeVelocity(locomotion::enc_vel);
  locomotion::lowPassFilter(locomotion::enc_vel);
  locomotion::set_locomotion_speed();
  feeding::maestro.setTargetMiniSSC(2, feeding::u8_rightFeedingServoPos);
  feeding::maestro.setTargetMiniSSC(3, feeding::u8_leftFeedingServoPos);
  locomotion::encoder.publish(&locomotion::i32_motorPosData);
  start::start.publish(&start::b_start);
  nh.spinOnce();
  delay(150);
}

#endif

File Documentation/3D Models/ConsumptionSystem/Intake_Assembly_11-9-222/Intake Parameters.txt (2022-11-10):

"ShaftDistance" = 2.5in

"SpokeDistance" = 1.75in

"D_Bearing" = 7 / 8in

"NumShaft" = 3

"Tol_Bearing" = 0.05in

"BearingHole" = "D_Bearing"+"Tol_Bearing"

"IntakeOpening" = "SpokeDistance"+1.75in

"SpokeLength" = 2in

"TempVariable"= 72

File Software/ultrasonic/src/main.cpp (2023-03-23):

/**
 * @file main.cpp
 * @author Nathan Gardner
 * @brief Main driver file
 * @version 0.2
 * @date 2023-01-21
 *
 * @copyright Copyright (c) 2023
 *
 */

#ifndef MAIN_CPP
#define MAIN_CPP

#include <Arduino.h>

#include <Ultrasonic.h>

Ultrasonic ultrasonic(7);
void setup()
{
 Serial.begin(9600);
}
void loop()
{
 long RangeInInches;
 long RangeInCentimeters;

 Serial.println("The distance to obstacles in front is: ");
 RangeInInches = ultrasonic.MeasureInInches();
 Serial.print(RangeInInches);//0~157 inches
 Serial.println(" inch");
 delay(250);

 RangeInCentimeters = ultrasonic.MeasureInCentimeters(); // two measurements should keep an interval
 Serial.print(RangeInCentimeters);//0~400cm
 Serial.println(" cm");
 delay(250);
}

#endif

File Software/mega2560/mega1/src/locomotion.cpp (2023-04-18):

#ifndef LOCOMOTION_CPP
#define LOCOMOTION_CPP

#include <Arduino.h>
#include <ros.h>
#include <util/atomic.h>

#include <geometry_msgs/Twist.h>
#include <std_msgs/Int32MultiArray.h>
#include <std_msgs/Float32MultiArray.h>

#include <locomotion.h>

namespace locomotion
{
// Locomotion Data
geometry_msgs::Twist t_stateMotorLocomotion;
std_msgs::Int32MultiArray i32_motorPosData;
// array format front_left, front_right, rear_left, rear_right
int32_t enc_pos[4] = { 0, 0, 0, 0 };
volatile int32_t enc_pos_i[4] = { 0, 0, 0, 0 };

float enc_vel[4] = { 0, 0, 0, 0 };
volatile float enc_vel_i[4] = { 0, 0, 0, 0 };
volatile float xyz[4] = { 0, 0, 0, 0 };

bool newDir = false;

float deltaT = 0;

std_msgs::Float32MultiArray af32_velocity;
ros::Publisher velocity("/locomotion/velocity", &af32_velocity);

// Locomotion Pub/Sub
ros::Publisher motorState("/locomotion/motorState", &t_stateMotorLocomotion);
ros::Publisher encoder("/locomotion/encoder", &i32_motorPosData);
ros::Subscriber<geometry_msgs::Twist> cmd_vel("/locomotion/cmd_vel", &cmdVelCallback);

void set_motor_speed(int motor_pin1, int motor_pin2, int speed_pin, int motor_speed)
{
  if (motor_speed > 0)
  {
    digitalWrite(motor_pin1, HIGH);  // forward direction
    digitalWrite(motor_pin2, LOW);
  }
  else if (motor_speed < 0)
  {
    digitalWrite(motor_pin1, LOW);  // reverse direction
    digitalWrite(motor_pin2, HIGH);
    motor_speed = -motor_speed;
  }
  else
  {
    digitalWrite(motor_pin1, LOW);  // stop movement
    digitalWrite(motor_pin2, LOW);
  }
  analogWrite(speed_pin, motor_speed);  // set motor speed (ignoring for now)
}

void cmdVelCallback(const geometry_msgs::Twist& cmd_vel)
{
  if(cmd_vel.linear.x != t_stateMotorLocomotion.linear.x ||
    cmd_vel.linear.y != t_stateMotorLocomotion.linear.y ||
    cmd_vel.angular.z != t_stateMotorLocomotion.angular.z){
    newDir = true;
  }
  t_stateMotorLocomotion = cmd_vel;
  // calculate motor speeds from twist message
  float x = cmd_vel.linear.x;
  float y = cmd_vel.linear.y;
  float z = cmd_vel.angular.z;

  float front_left_speed = y + x + z;
  float front_right_speed = y - x - z;
  float rear_left_speed = y - x + z;
  float rear_right_speed = y + x - z;
  
  xyz[0] = front_left_speed;
  xyz[1] = front_right_speed;
  xyz[2] = rear_left_speed;
  xyz[3] = rear_right_speed;
}

void set_locomotion_speed()
{
  // variable which will hold the pwr (-255 to 255) which will be written to the motors, (front left, front right, rear left, rear right)
  int pwr[4];
  pi_control(enc_vel, pwr, xyz);
  
  // set motor speeds
  set_motor_speed(FRONT_LEFT_PIN1, FRONT_LEFT_PIN2, FRONT_LEFT_SPEED_PIN, pwr[0]);
  set_motor_speed(FRONT_RIGHT_PIN1, FRONT_RIGHT_PIN2, FRONT_RIGHT_SPEED_PIN, pwr[1]);
  set_motor_speed(REAR_LEFT_PIN1, REAR_LEFT_PIN2, REAR_LEFT_SPEED_PIN, pwr[2]);
  set_motor_speed(REAR_RIGHT_PIN1, REAR_RIGHT_PIN2, REAR_RIGHT_SPEED_PIN, pwr[3]);
}

void updateEncoder()
{
  ATOMIC_BLOCK(ATOMIC_RESTORESTATE)
  {
    for (int i = 0; i < 4; i++)
    {
      enc_pos[i] = enc_pos_i[i];
    }
  }
  i32_motorPosData.data_length = sizeof(enc_pos) / sizeof(enc_pos[0]);
  i32_motorPosData.data = enc_pos;
}

void updateVelocity()
{
  ATOMIC_BLOCK(ATOMIC_RESTORESTATE)
  {
    for (int i = 0; i < 4; i++)
    {
      enc_vel[i] = enc_vel_i[i];
    }
  }
  af32_velocity.data_length = 4;
  af32_velocity.data = enc_vel;
}

void readFrontLeftEncoder()
{
  int b = digitalRead(FRONT_LEFT_ENCB);
  if (b > 0)
  {
    enc_pos_i[0]++;
  }
  else
  {
    enc_pos_i[0]--;
  }
}

void readFrontRightEncoder()
{
  int b = digitalRead(FRONT_RIGHT_ENCB);
  if (b > 0)
  {
    enc_pos_i[1]--;
  }
  else
  {
    enc_pos_i[1]++;
  }
}

void readRearLeftEncoder()
{
  int b = digitalRead(REAR_LEFT_ENCB);
  if (b > 0)
  {
    enc_pos_i[2]++;
  }
  else
  {
    enc_pos_i[2]--;
  }
}

void readRearRightEncoder()
{
  int b = digitalRead(REAR_RIGHT_ENCB);
  if (b > 0)
  {
    enc_pos_i[3]--;
  }
  else
  {
    enc_pos_i[3]++;
  }
}

void computeVelocity(volatile float* vel)
{
  static int32_t enc_posPrev[4];
  static long prevT;
  long currT = micros();
  deltaT = ((float)(currT - prevT)) / 1.0e6;
  for (int i = 0; i < 4; i++)
  {
    *(vel + i) = (enc_pos[i] - enc_posPrev[i]) / deltaT;
    // convert from clicks per cycle to rpm
    *(vel + i) = *(vel + i) / CLICKS_PER_ROTATION * 60.0;

    enc_posPrev[i] = enc_pos[i];
  }
  prevT = currT;
}

void lowPassFilter(volatile float* vel)
{
  static float velocityFilter[4];
  static float velocityPrev[4];
  for (int i = 0; i < 4; i++)
  {
    // predefined low pass filter constaints
    velocityFilter[i] = 0.854 * velocityFilter[i] + 0.0728 * (*(vel + i)) + 0.0728 * velocityPrev[i];
    velocityPrev[i] = *(vel + i);
  }
  // update velocity to low pass filter version
  vel = velocityFilter;
}

void pi_control(float* vel, int* pwr, volatile float* xyz)
{
  static float eintegral[4];
  static float ederivative[4];
  static float prevE;

  if(newDir){
    eintegral[0] = 0;
    eintegral[1] = 0;
    eintegral[2] = 0;
    eintegral[3] = 0;
    ederivative[0] = 0;
    ederivative[1] = 0;
    ederivative[2] = 0;
    ederivative[3] = 0;

    newDir = false;
  }

  float kp = 1.5;
  float ki = 3;
  float kd = 0;

  
  for (int i = 0; i < 4; i++)
  {
    float vt = *(xyz + i);
    float e = vt - *(vel + i);
    eintegral[i] = eintegral[i] + e * deltaT;
    ederivative[i] = (e - prevE)/deltaT;
    float u = e * kp + eintegral[i] * ki + ederivative[i] * kd;
    *(pwr + i) = (int)u;
    // cap pwr at -255 or 255
    if (*(pwr + i) > 255)
    {
      *(pwr + i) = 255;
    }
    else if (*(pwr + i) < -255)
    {
      *(pwr + i) = -255;
    }
    prevE = e;
  }
}

void e_stop(){
  set_motor_speed(FRONT_LEFT_PIN1, FRONT_LEFT_PIN2, FRONT_LEFT_SPEED_PIN, 0);
  set_motor_speed(FRONT_RIGHT_PIN1, FRONT_RIGHT_PIN2, FRONT_RIGHT_SPEED_PIN, 0);
  set_motor_speed(REAR_LEFT_PIN1, REAR_LEFT_PIN2, REAR_LEFT_SPEED_PIN, 0);
  set_motor_speed(REAR_RIGHT_PIN1, REAR_RIGHT_PIN2, REAR_RIGHT_SPEED_PIN, 0);
}
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

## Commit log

2022-06-27 Updated electrical schematic
    [PedestalStorageCapstone.kicad_sch]
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2022-09-22 uploading timeline created for project proposal
    [CapstoneTimeline.xlsx]
2022-09-22 updated the timeline
    [CapstoneTimeline.xlsx]
2022-10-16 updated gantt chart
    [CapstoneTimeline.xlsx]
2022-10-16 added assignees for conceptual design
    [CapstoneTimeline.xlsx]
2022-10-26 updated timeline in excel
    [CapstoneTimeline.xlsx]
2022-10-29 Updated Timeline/Gantt Chart
    [CapstoneTimeline (1).xlsx]
2022-10-29 changed timeline name
    [CapstoneTimeline (1).xlsx, CapstoneTimeline.xlsx]
2022-10-29 Updated Timeline/Gantt Chart Pt 2
    [CapstoneTimeline.xlsx]
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2022-11-10 3d models added
    [1277N28_Corrosion-Resistant Timing Belt Pulley.SLDPRT, 1277N41_Corrosion-Resistant Timing Belt Pulley.SLDPRT, 25d-metal-gearmotor-34-47-encoder.step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]
2022-11-14 fixed eqns to be inline, need to check gear ratio
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2022-11-16 fixed torque calculation
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2022-11-20 correct torque number in shear explaination
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2022-11-22 added sch files
    [ObjectConsumption.kicad_pcb, ObjectConsumption.kicad_sch]
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2022-11-30 Update MarkBeech-signoff-Sorting.md
    Added a few constraints about the flipper and color sensor
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2022-12-02 Added CAD files for the wheel and motor mount
    [48MM Steel Mecanum Wheel 14209.STEP, pololu-25d-mm-metal-gearmotor-bracket.step]
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2022-12-02 added schematic files, reorg file structure
    [ControllerSubsystem.kicad_pcb, ControllerSubsystem.kicad_sch, ObjectConsumption.kicad_pcb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]
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2022-12-03 removed models of the wheel, motor, and mount
    [25d-metal-gearmotor-34-47-encoder.step, 48MM Steel Mecanum Wheel 14209.STEP, pololu-25d-mm-metal-gearmotor-bracket.step]
2022-12-03 added circuit schematic
    [circuitSchematic.kicad_sch]
2022-12-03 added wheel/motor assembly CAD model
    [Motor_Wheel_Assembly.SLDASM]
2022-12-03 added duck and pedestal electrical sch
    [ElectricalSchematicforStorage.kicad_pcb, ElectricalSchematicforStorage.kicad_sch]
2022-12-03 changed file name
    [ElectricalSchematicforStorage.kicad_pcb, ElectricalSchematicforStorage.kicad_sch]
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2022-12-03 addressed changes
    [ElectricalSchematicforStorage.kicad_sch]
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2022-12-04 added sorting electrical schematics
    [SortingSubsystem.kicad_pcb, SortingSubsystem.kicad_sch]
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2022-12-04 added schematic file
    [SortingSubsystem.kicad_sch]
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2023-01-10 updated circuit schematic
    [locomotion_circuitSchematic.kicad_sch]
2023-01-11 removed old circuit schematic
    [locomotion_circuitSchematic.kicad_sch]
2023-01-11 added new circuit schematic
    [Locomotion.kicad_pcb, Locomotion.kicad_sch]
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2023-01-15 added new 3D model and pics
    [Locomotion.SLDASM]
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2023-01-20 Fixed BOM
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2023-01-20 added BOM file and analysis
    [Consumption_BOM.xlsx]
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2023-01-20 Fixed the electrical schematic
2023-01-24 Consumption Control Mega2560 (#31)
    * added consumption control ros node
    * changed msg type from bool to uint8 for motor cmd
    * removed unneeded code
    * ranamed topics for clarity
    * updated comment
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2023-01-26 added kicad files
    [VisionSystem.kicad_pcb, VisionSystem.kicad_sch]
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2023-01-27 more specific and added Pull up resistor
    [VisionSystem.kicad_sch]
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2023-01-27 fixed links to schematic and 3D model
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2023-01-29 fixed schematic
    [VisionSystem.kicad_sch]
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2023-02-06 Deleted outdated 3d models
    [57655K62_14-1 2 Degree Pressure Angle Gear Rack (1).SLDPRT]
2023-02-06 Removed old electrical schematics
    [ElectricalSchematicforStorage.kicad_pcb, ElectricalSchematicforStorage.kicad_sch]
2023-02-06 added solidworks file
    [Cylinder_stacker_final.SLDASM]
2023-02-06 added electrical schematic files
    [Feeding Schematic.kicad_pcb, Feeding Schematic.kicad_sch]
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2023-02-07 added chassis fit files
    [Aduino.ipt, Arduino2.ipt, Assembly2.iam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]
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2023-02-07 Fixed BOM, added torque calculation for servo
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2023-02-08 added updated chassis fit CAD models
    [Assembly2.iam, ToF Sensor.ipt, ToF Sensor2.ipt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]
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2023-02-08 fixed table, analysis, and BOM
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2023-02-08 Deleted old circuit schenatic and added updated
    [PedestalStorageCapstone.kicad_pcb, PedestalStorageCapstone.kicad_sch]
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2023-02-09 Added images for buck noise simulations
2023-02-10 added correct component values to schematic
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2023-02-10 fixed analysis for sensor
2023-02-10 fixed sensor analysis
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2023-02-10 fixed electrical schematic
2023-02-10 actually fixed electrical schematic
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2023-02-10 schematic update
    [SortingSubsystem.kicad_sch]
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2023-02-10 changed electrical schematic
    [SortingSubsystem.kicad_sch]
2023-02-10 edited schematic
    [SortingSubsystem.kicad_sch]
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2023-02-13 update schematic
    [VisionSystem.kicad_sch]
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2023-02-13 update sch
    [VisionSystem.kicad_sch]
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2023-02-14 fixed BOM...again
2023-02-15 added final total BOM
    [TotalBOM_Final.xlsx]
2023-02-15 added final BOM
    [TotalBOM_Final.xlsx]
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2023-03-02 feature_locomotionControl (#36)
    * git init add locomotion function
    * added locomotion Twist messages
    * added adjustable speed
    * added doxygen documentation
    * added encoder readings
    * added array topic for encoder vales
    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
2023-03-10 feature_Feeding (#38)
    * added maestro library
    * servo working w/o ros
    * rework servo write
    * servo working w/ ros
    * added docs
    * refactored everything
    * added docs
    * clang format
    * refactor
    [consumption.cpp, consumption.h, feeding.cpp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]
2023-03-23 Ultrasonic demo to main (#41)
    * init commit
    * Delete Software/mega2560/mega2 directory
2023-04-01 Feature PID controller for locomotion control (#39)
    * got velocity in counts / sec
    * added pi_control, lowPassFilter
    * improved pi controller
    * fixed pi controller, working now
    * addressed comments
    * added documentation
    * documentation and clang-format
    * addressed comments
    * update docs
    * changed delay in main
    * added volatile for cmd_vel callback
    * increase baud rate and removed unneeded pubs
    * update for new chassis
    * increased delay, created ramp time for motor control, comment out unneeded pub/sub
    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
    [consumption.cpp, feeding.cpp, locomotion.cpp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]
2023-04-01 feature_duckstorage_solenoid_servo (#43)
    * added servo
    * added ROS for mega2
    * nh.initNode(); is added
    * changed to Serial2 and Bool for solenoid
    * added solenoid control in ros
    * merge diff to mega1
    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
2023-04-07 added eintegral reset, removed setpoint grad increase, changed max error count
    [locomotion.cpp, locomotion.h]
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2023-04-20 Experimental Analysis (#49)
    * constraints from signoffs, measures of success
    * removed non-implemented subsystems
    * added locomotion and feeding experimental analysis
    * addressed consumption and duck s and d
    * addressed spoke material
    * Added shall statements at bottom of document
    * format error
    * addressed measures of success, sorted shalls
    * Formatting changes
    * wording
    * mentioned recycling in measures of success
    * Added section for cut subsystems and justification
    * formatting error
    * power constraints
    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
2023-04-23 GitHub enhancements before publication (#48)
    * update README.md
    * update FinalBOM excel sheet
    * update TotalBOM_final.xlsx
    * Update README title
    * update Salient Outcomes
    * added image to README.md
    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
    [Experimental_Analysis.xlsx, ME_BOM.ods, TotalBOM_Final.xlsx]
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2023-04-24 updated BOM for parts used
    [TotalBOM_Final.xlsx]
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2023-04-24 fixed image problem power E2
